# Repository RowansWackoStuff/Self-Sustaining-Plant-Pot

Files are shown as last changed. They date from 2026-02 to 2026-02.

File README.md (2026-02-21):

# SelfSustainingPlantPot
This project is an attempt at making a self watering plant pot that can water plants overtime with custom settings

Goals:
- enough water to last a week
- supplied by battery power
- release water consistently
bonus goals:
- controlled through web server
- setting for watering seeds over time

I wanted to start with a pot that contains the soil and the electronic components, which could have an external silo attached that could be filled with water. The pot diameter has to be at least 15 cm and the height must be 15cm in order for proper root development. With this in mind, a rough sketch can be made.
<div align="center">
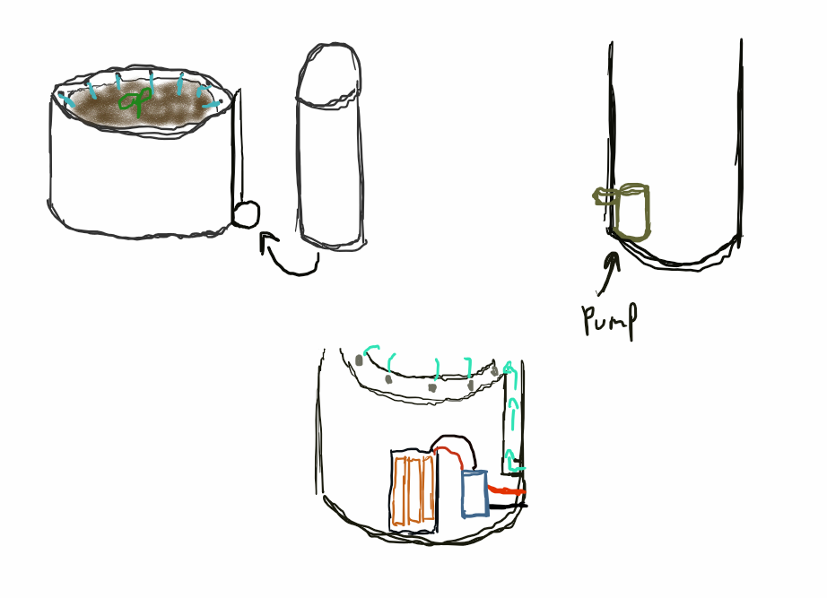
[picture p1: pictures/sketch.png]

</div>

## Piping

The first step was to find out how the water pipe setup would be done. In order to do this i started by testing different pipe hole diameters, number of holes and pipe lengths until I found the desired pressure.

<div align="center">
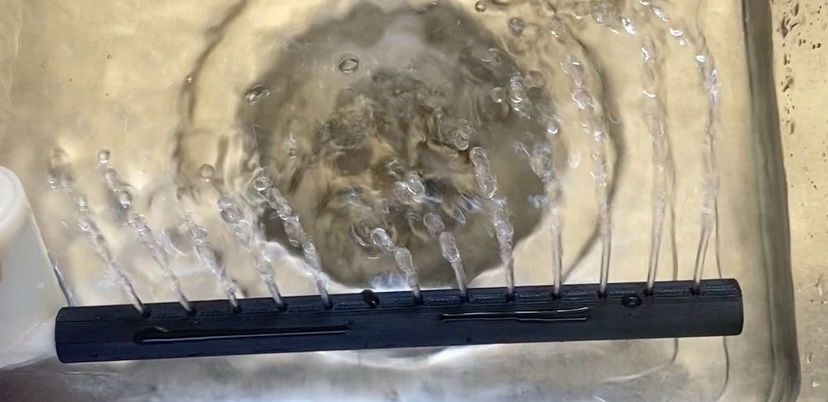
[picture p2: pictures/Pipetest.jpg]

</div>

After some trial and error, the number of holes and diameter were determined and made into a ring.

<div align="center">
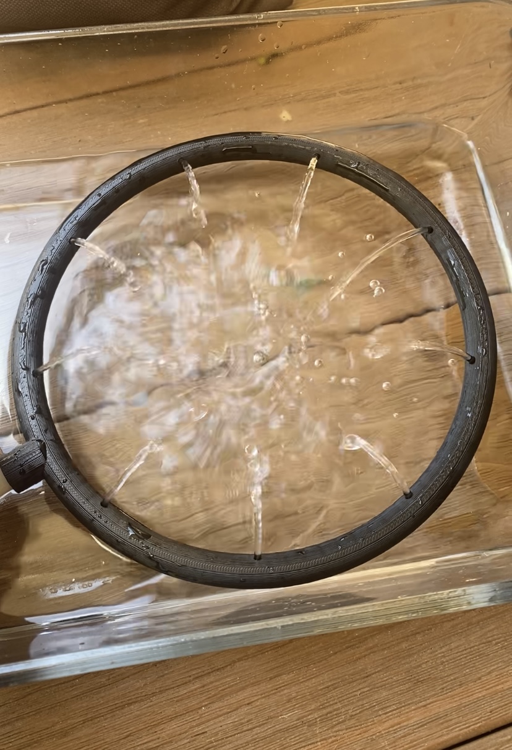
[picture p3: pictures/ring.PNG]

</div>

Adding an extension pipe from the pump to the ring reduces the amount of pressure in the piping, so I assumed I would need to alter the ring's hole's size but the pressure was sustainable enough to travel the distance and exit the holes perfectly.
(This one was a bit over the top.)
<div align="center">
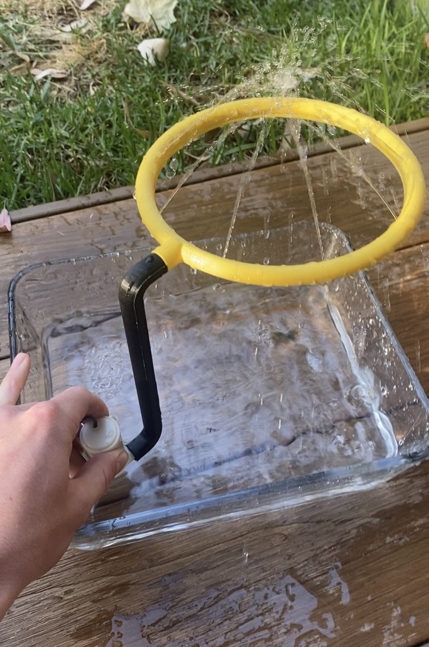
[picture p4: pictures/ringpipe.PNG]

</div>

## Electronics
The electronics involved would have to be a power supply, a microcontroller and a small water pump. For the microcontroller, I chose the ESP32-c3 supermini for its size and web hosting capabilities. 

The power supply for the ESP32 needed a minimum of 3.3V and had to last a long period of time. With the ESP consuming 0.4 mA per hour at most in deep sleep and the estimated time for a lettuce to mature being at most 11 weeks (77 days, 1,848 hours), then the power supply needs 0.004 * 1,848 = 7392 mAh

Using a configuration of 3 AA batteries in series the collective voltage is 4.5V and has a current supply of 8,100mah satisfying the needs of the system

Starting out I used a transistor to deliver 5V to the pump through the board. This setup didn't work due to the poor flow of current through the resistor limiting the output of the water pump.
<div align="center">
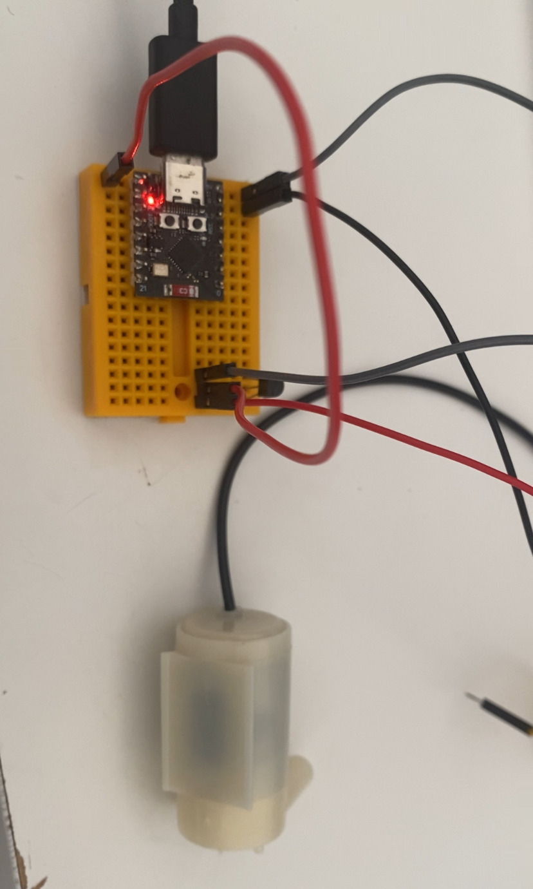
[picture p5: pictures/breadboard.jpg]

</div>

In order to fix this issue, I swapped the transistor for a relay with an external power supply. This solution also solved the voltage drop the ESP was suffering from, which caused it to reset every time the motor turned on.
<div align="center">
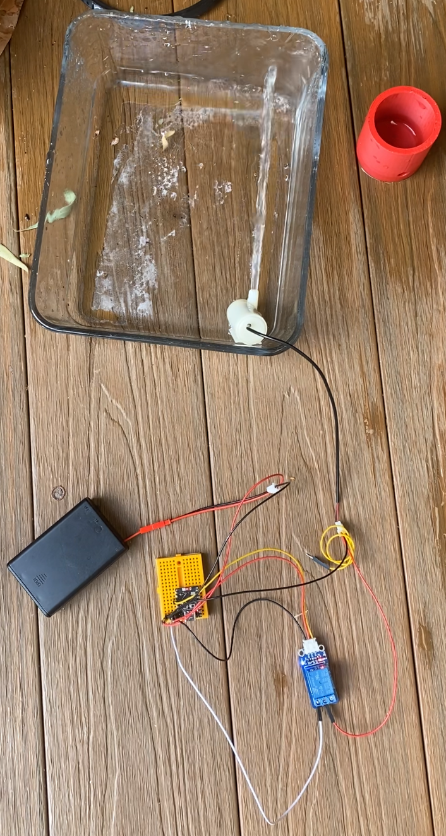
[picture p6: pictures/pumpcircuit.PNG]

</div>

## Programming

In order to interact with the system, I used the ESPAsyncWebServer library, which allowed for the ESP to run an asynchronous web server off its wifi. This wifi can be connected with through any device in order to open a webpage containing the user interface of the system.

This user interface consists of a water setting for default watering a plant daily with the same amount aswell as a seed setting the takes a minimum and maximum amount of water as well as the amount of days to water in order to grow seeds. The seeds are watered exponentially over the day's as in the early stage of development the seeds need a small amount of water, and in the mature stages require a drastically larger amount of water.

<div align="center">
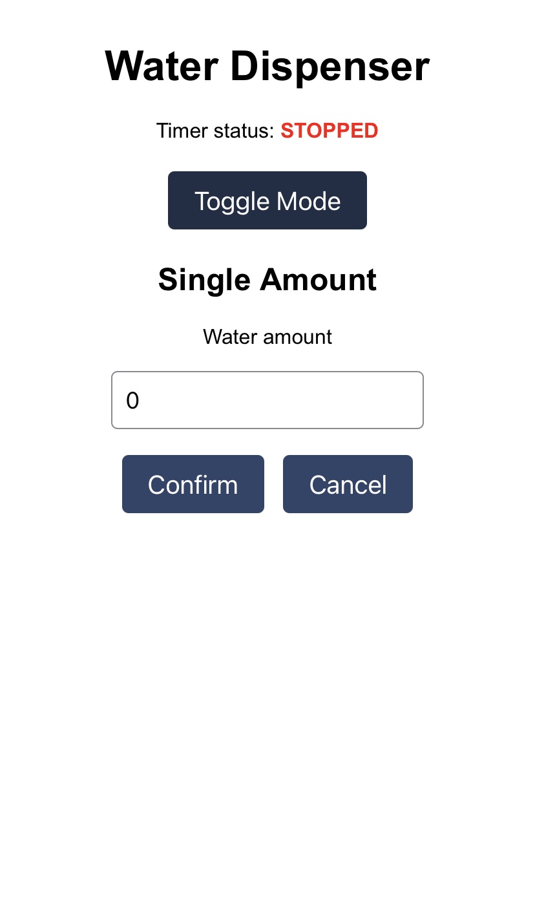
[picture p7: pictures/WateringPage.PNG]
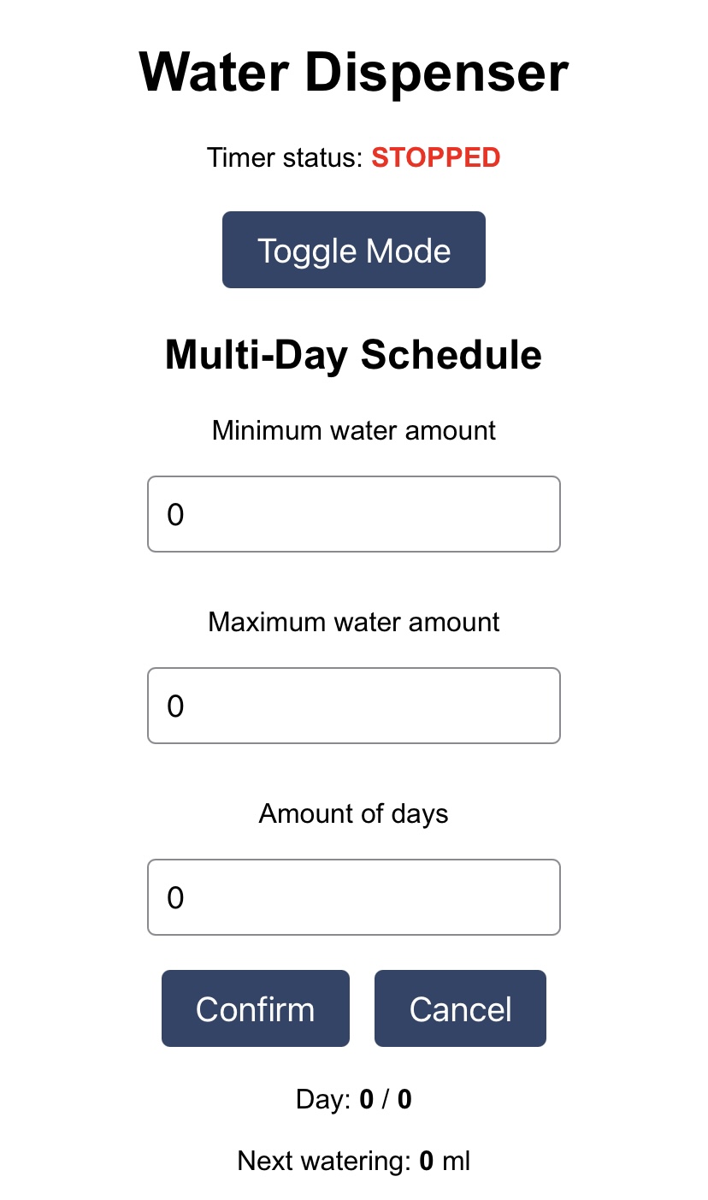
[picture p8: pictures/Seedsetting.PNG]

</div>

Deep sleep is an ultralow power state for microcontrollers that maximizes the amount of battery life when waiting. For the pot, the deep sleep is set once the watering settings are set and the switch for pin 5 is off. This turns off the wifi and other components and sets a 24hr timer for the system to wake up, water, sleep and repeat. With this programming running in the startup script of the esp the system can save power and extend the project's lifetime.

## Testing pot
A small lettuce needs roughly less than 1 cup of water a day for growth. With this in mind, the height of the reservoir can be calculated.

1 cup = 250ml, 7 cups = 1750ml, 1750ml = 1750cm^3, cylinder volume = pi*r^2*h, 1750cm = pi * 7.5^2 * h, h = 9.9cm

With this, the height of the reservoir will be rounded to 10 cm.

I wanted the pot to be modular in order to print in the printer's base of 256x256mm. In order to do this, I split the pipe, ring, reservoir, pot, and electrical components into seperate moduals.

## TEST POT
I printed and tested each part individually and avoided printing the top pot in order to save filiment and instead just printed the base screw and ring mount seperatly.
<div>
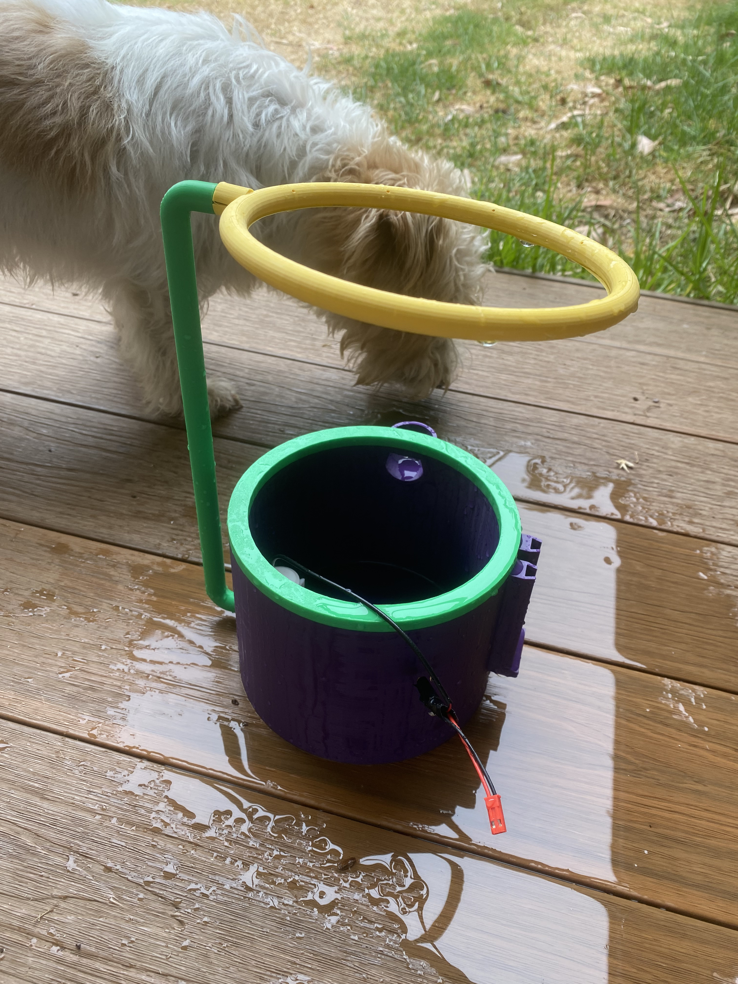
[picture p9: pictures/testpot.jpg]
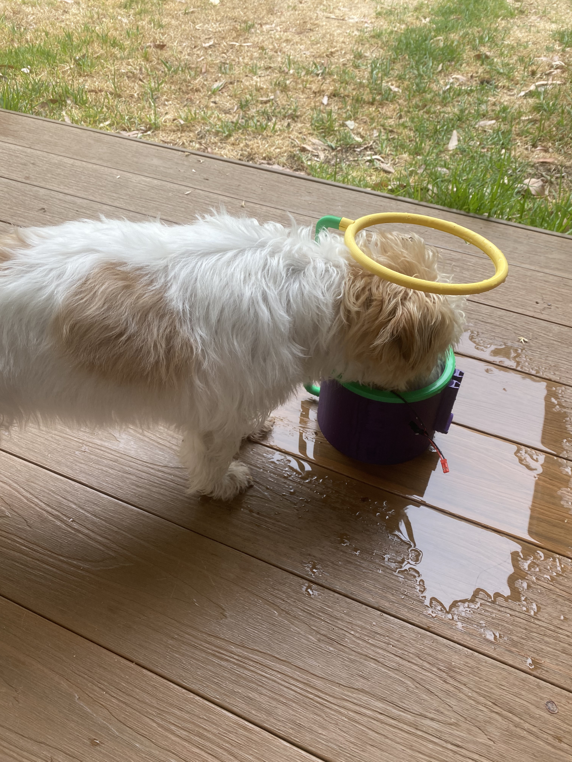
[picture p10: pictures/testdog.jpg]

</div>

## FINAL MODELS

## Ring + Pipe
The ring connects into the top of the pot to keep it still, with the pipe having connections to the reservoir and ring.
<div align="center">
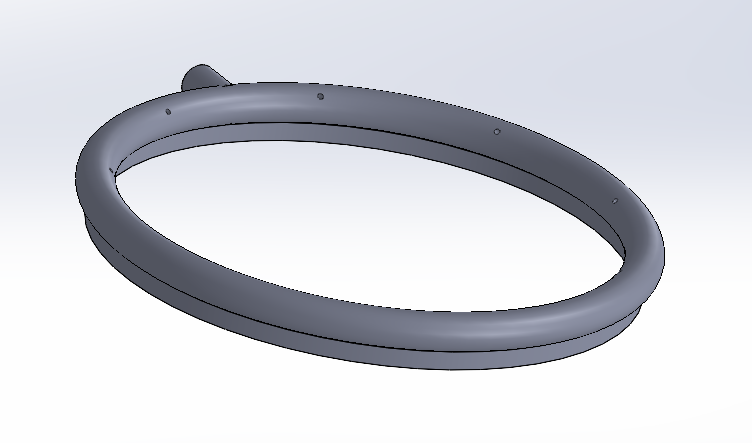
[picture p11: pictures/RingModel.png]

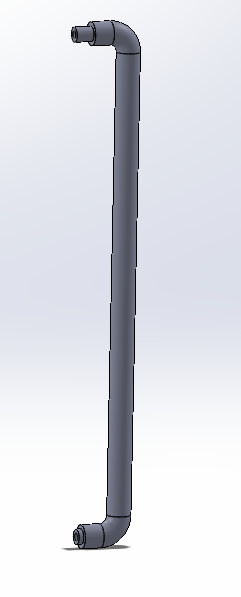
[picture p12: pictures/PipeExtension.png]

</div>

## Top Pot
The top pot has a custom screw base as well as a circular cut in the top to allow for a stable ring connection.
<div align="center">
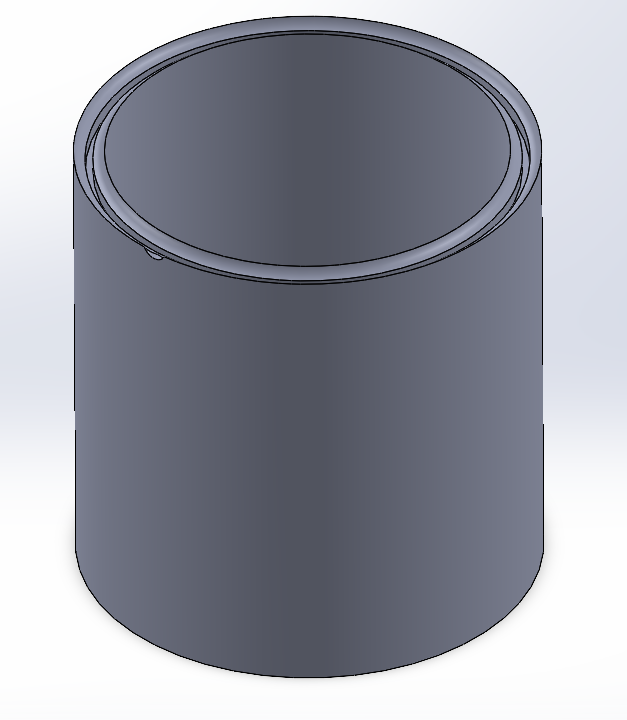
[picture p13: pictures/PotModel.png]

</div>

## Reservoir
The reservoir has the connection to the battery box to slide into as well as a hole for the pump's pipe to slot into.
<div align="center">
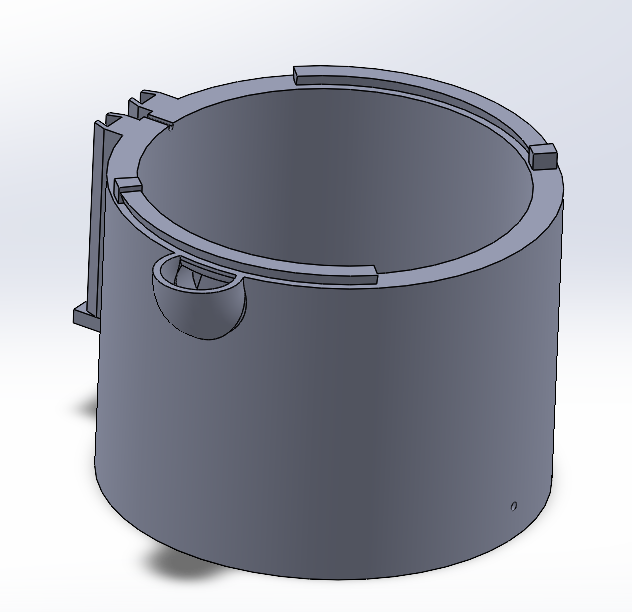
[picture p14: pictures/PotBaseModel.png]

</div>

## Battery Box
The battery box is built of several parts that slide into place with each other before slotting into the reservoir. The battery box has space to hold 6 double A batteries, with the circuit box attaching on top for all the electrical components to sit inside.
<div align="center">
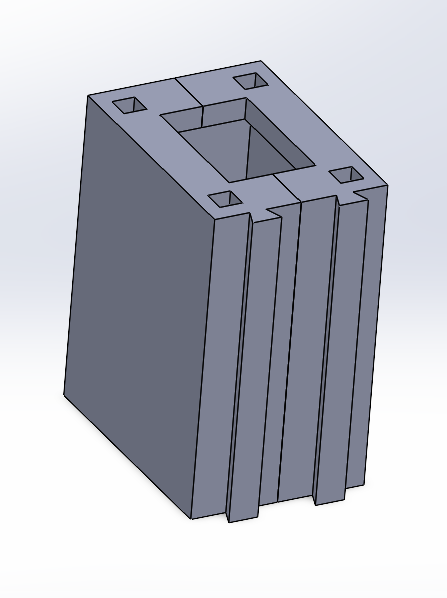
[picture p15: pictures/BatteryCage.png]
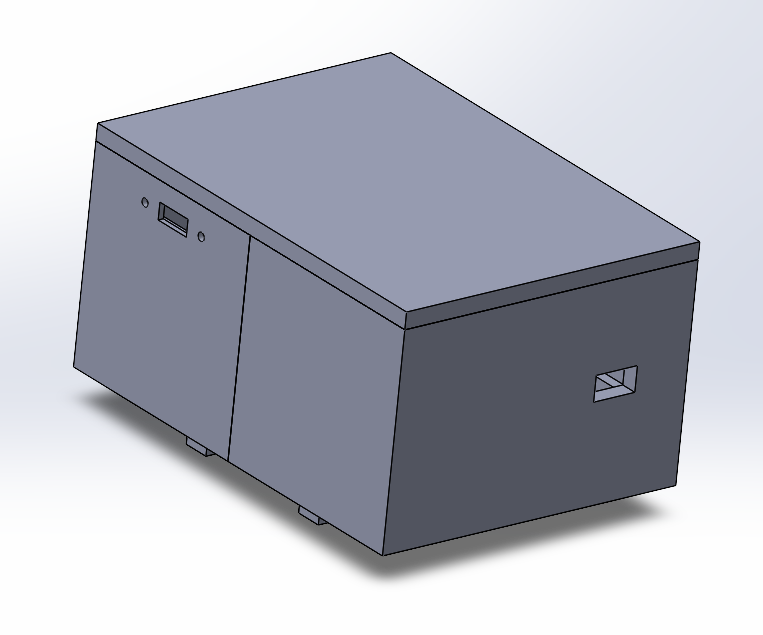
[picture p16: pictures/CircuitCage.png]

</div>

## FINISHED

<div align="center">
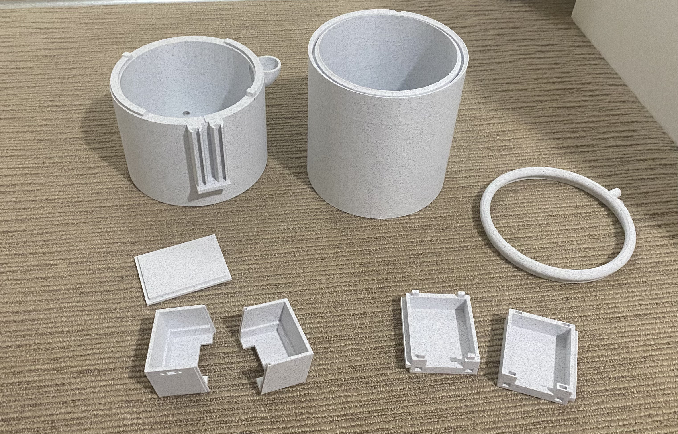
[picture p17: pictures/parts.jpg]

</div>

<div align="center">
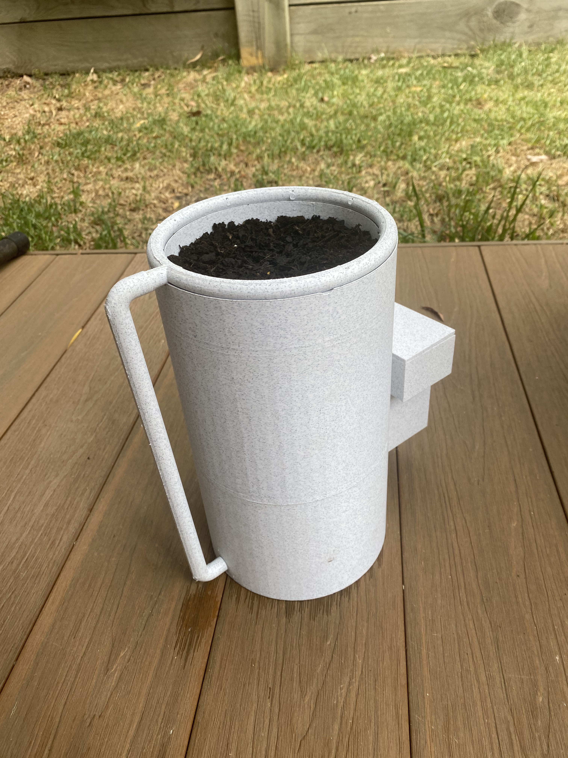
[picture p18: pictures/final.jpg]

</div>

# Conclusion

Goals:
- enough water to last a week ✅
- supplied by battery power ✅
- release water consistently ✅
Bonus goals:
- controlled through web server ✅
- setting for watering seeds over time ✅

# mistakes/problems on the way
- SolidWorks having no export only save as led me to save over my own files multiple times instead of exporting stls
- printed the final prototype base just for it to come out missing the pipe connection in order to not waste filiment printing again I drilled a hole
in the same place, this caused me to have to remake the extension pipe as well as caused the pump to be superglued in place due to it being loose in the hole (wont be making that mistake again)
- the external pipe leaks due to poor sealing
- Tolerance for filiments changed when swapping to the final prototype so testing the connections was a waste of time

# Improvements for Next Time:
- reduce locking seal length (friction is very strong).
- get external clock from the esp as the esp couldn't track how longs it's slept for.
- improve seals for water pipes.
- Incorporate pipe into waterpot for better aesthetic.
- Create a custom PCB to reduce soldering errors.
- Battery box clips separated (need to learn better techniques)
- Sort SolidWorks files neatly in order to reduce complications
  
I'll update this page with the lettuce growth once complete (if ever).

THANKS FOR READING!

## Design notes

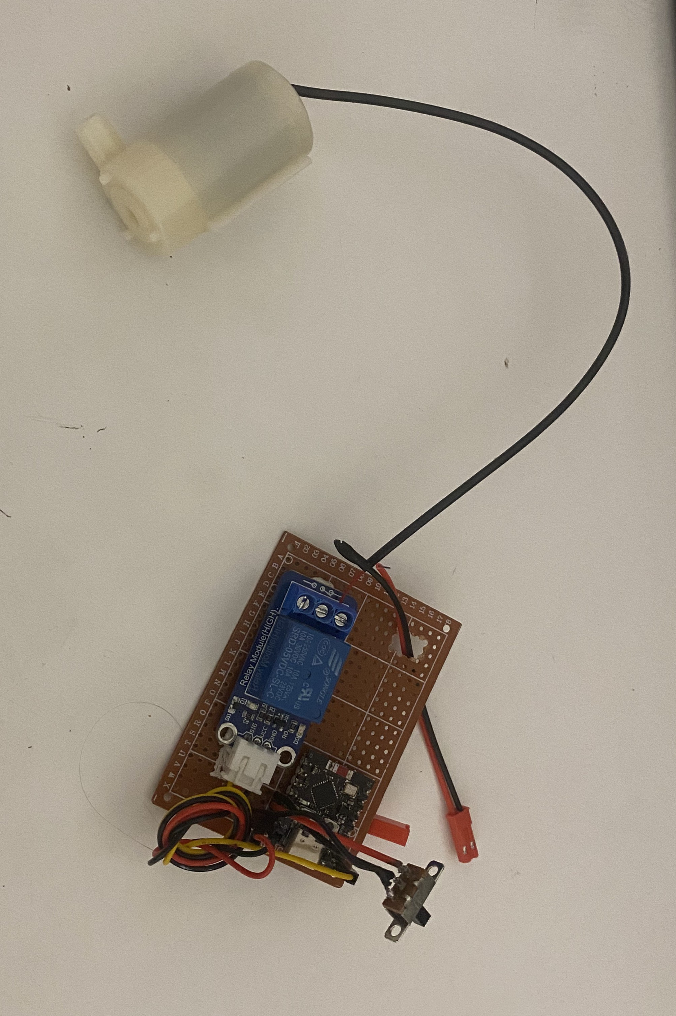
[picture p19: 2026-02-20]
pictures/circuit.jpg

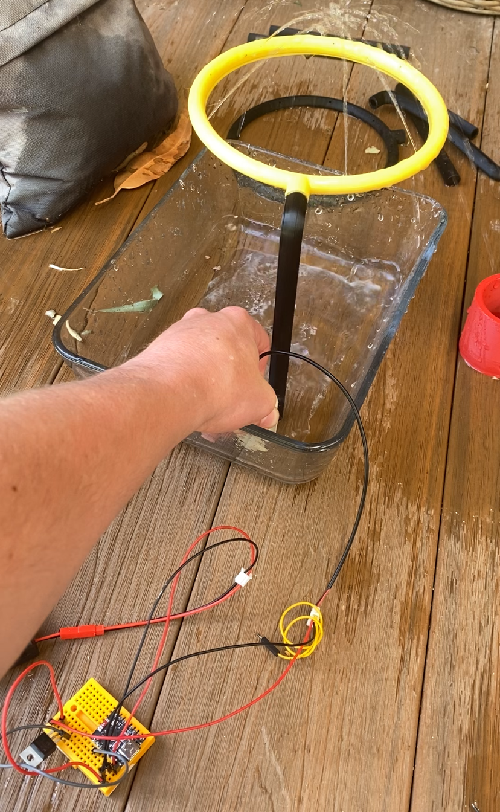
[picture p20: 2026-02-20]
pictures/ringpipecircuit.PNG

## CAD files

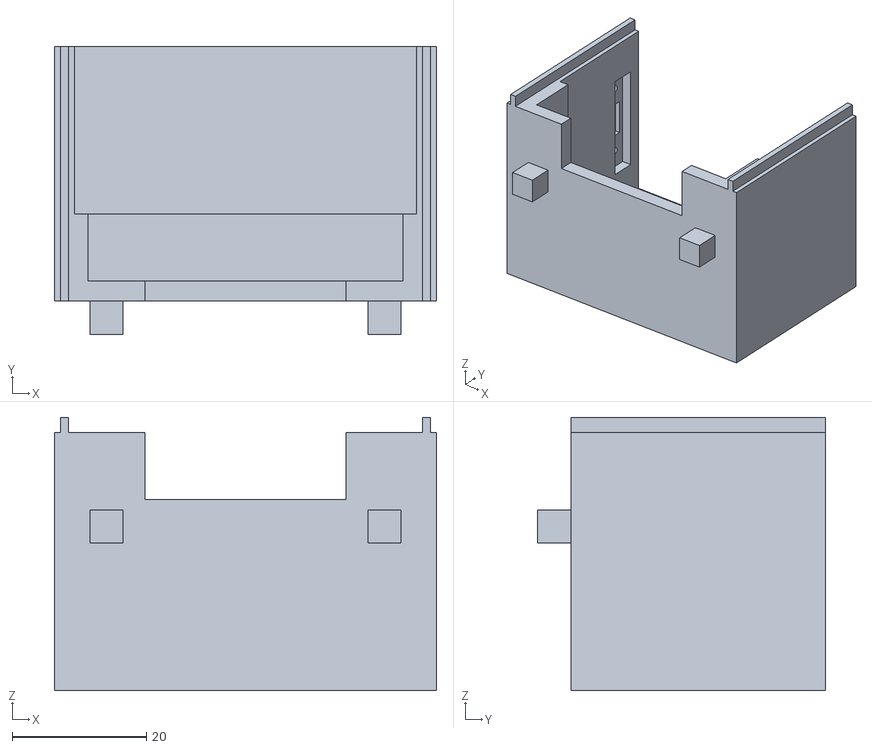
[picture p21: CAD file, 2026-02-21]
SolidWorksFiles/CircuitCage1.STL
57.0 x 43.0 x 40.8

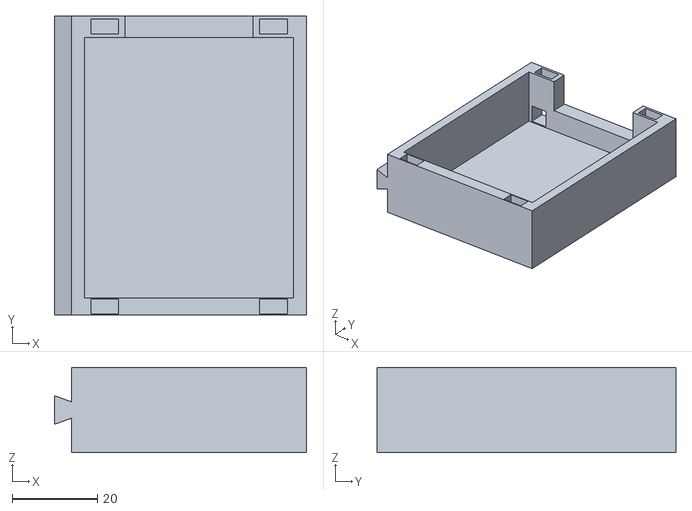
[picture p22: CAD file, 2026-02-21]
SolidWorksFiles/BatteryCage1.STL
59.0 x 70.0 x 20.0

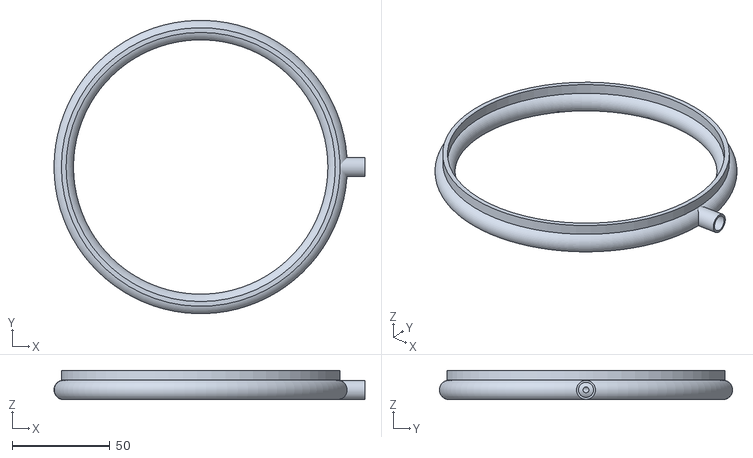
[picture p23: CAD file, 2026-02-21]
SolidWorksFiles/ringTest10.STL
159.0 x 149.9 x 15.0

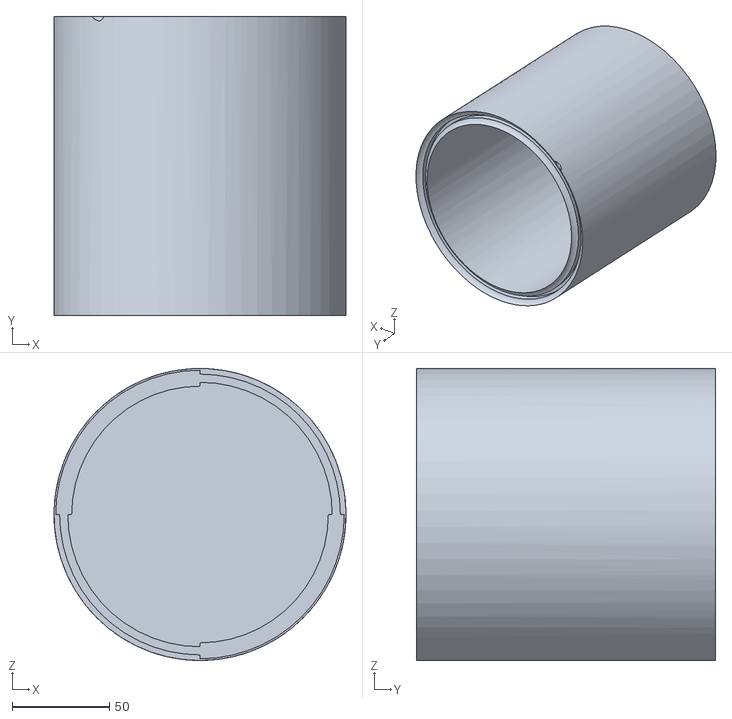
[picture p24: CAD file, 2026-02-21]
SolidWorksFiles/PotTopFINAL.STL
150.0 x 153.7 x 150.0

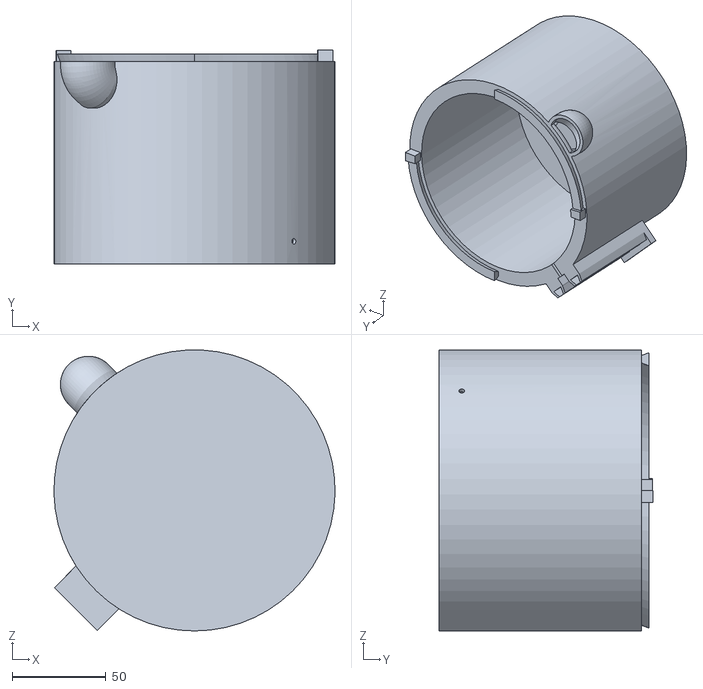
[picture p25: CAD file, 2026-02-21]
SolidWorksFiles/PotBaseTest.STL
149.9 x 114.0 x 149.9

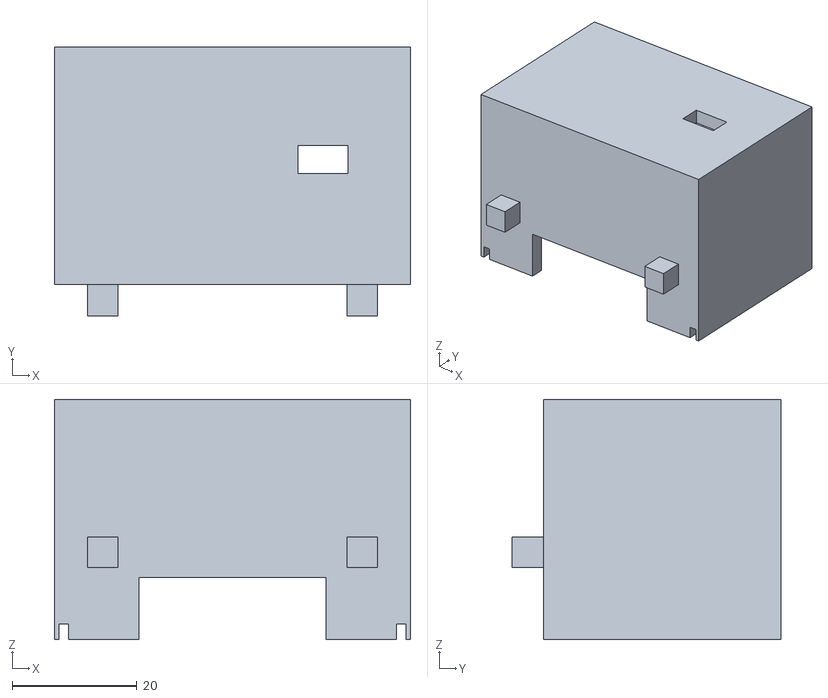
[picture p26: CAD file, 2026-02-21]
SolidWorksFiles/CircuitCage2.STL
57.0 x 43.0 x 38.5

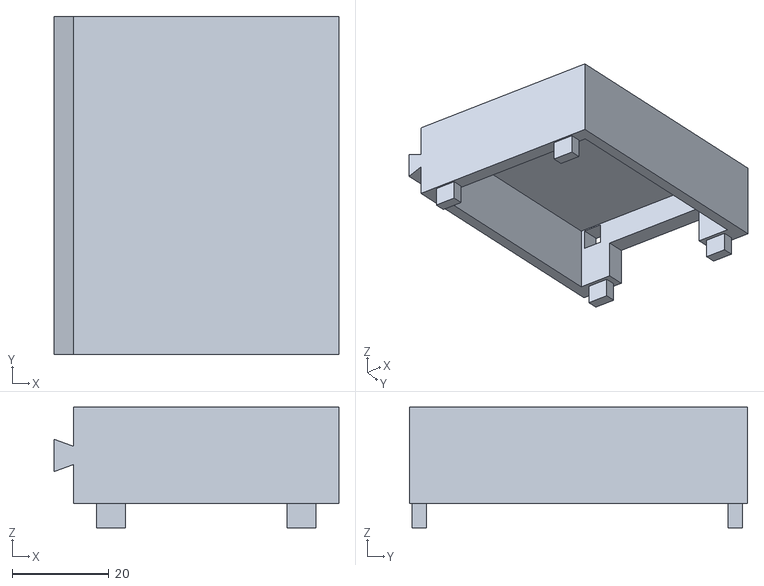
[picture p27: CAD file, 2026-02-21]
SolidWorksFiles/BatteryCage2.STL
59.0 x 70.0 x 25.0

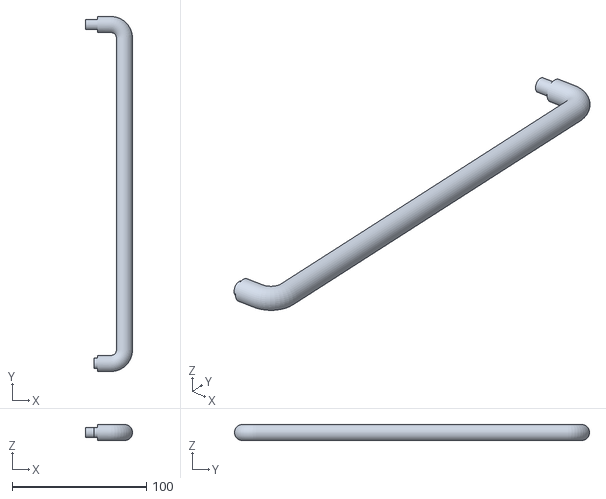
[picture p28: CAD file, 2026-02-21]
SolidWorksFiles/pipeExtensionFIX2.STL
35.0 x 264.0 x 12.0

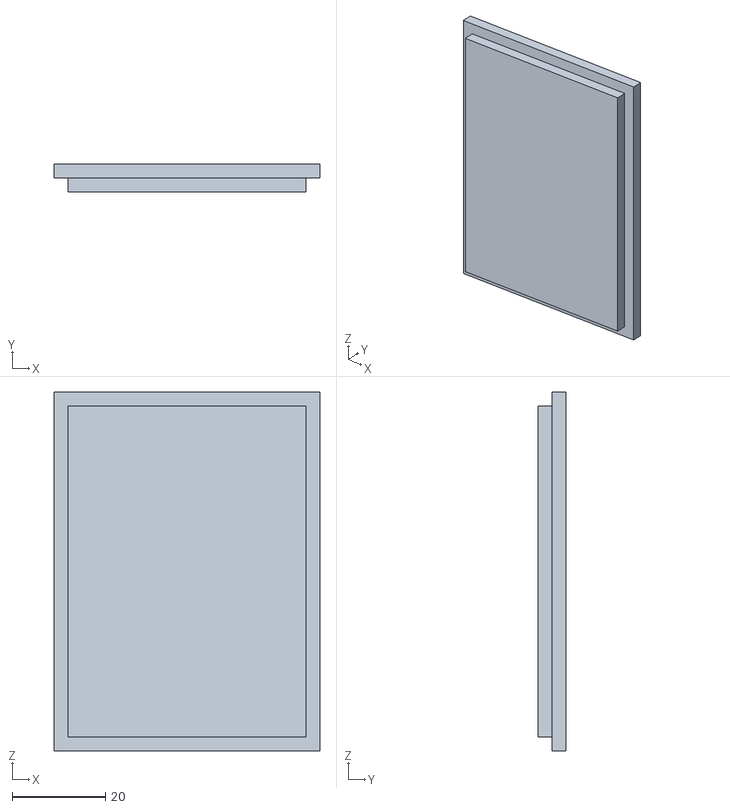
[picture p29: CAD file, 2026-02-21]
SolidWorksFiles/CircuitCage3.STL
57.0 x 6.00 x 77.0

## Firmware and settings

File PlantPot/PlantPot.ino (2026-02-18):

#include <Arduino.h>
#include "esp_sleep.h"

#include <WiFi.h>
#include <AsyncTCP.h>
#include "esp_sleep.h"
#include <ESPAsyncWebServer.h>

#define BUTTON_PIN 4 // RTC-capable pin

const int pumpPin = 5; 

bool pumpRunning = false;
unsigned long pumpStopTime = 0;

const unsigned long TIMER_24H = 24UL * 60ULL * 60ULL * 1000000ULL;
// const unsigned long TIMER_24H = 15ULL * 1000000ULL;

RTC_DATA_ATTR double waterAmount = 0;
RTC_DATA_ATTR double maxWaterAmount = 0;
RTC_DATA_ATTR double days = 0;
RTC_DATA_ATTR double currentDay = 0;
RTC_DATA_ATTR bool seedSettingActive = false;
RTC_DATA_ATTR bool timer24hActive = false;

// HTML web page
const char index_html[] PROGMEM = R"rawliteral(
<!DOCTYPE HTML><html>
<head>
  <title>ESP Water Control</title>
  <meta name="viewport" content="width=device-width, initial-scale=1">
  <style>
    body { font-family: Arial; text-align: center; margin:0 auto; padding-top: 20px;}
    input {
      padding: 10px;
      font-size: 18px;
      width: 220px;
      margin-bottom: 15px;
    }
    .button {
      padding: 10px 20px;
      font-size: 20px;
      color: #fff;
      background-color: #2f4468;
      border: none;
      border-radius: 5px;
      cursor: pointer;
      margin: 5px;
    }
    .button:hover { background-color: #1f2e45; }
    .hidden { display: none; }
  </style>
</head>
<body>
  <h1>Water Dispenser</h1>

  <p>
    Timer status:
    <strong id="timerStatus" style="color:red;">STOPPED</strong>
  </p>

  <button class="button" onclick="togglePage()">Toggle Mode</button>

  <!-- PAGE 1 -->
<div id="pageSingle">
  <h2>Single Amount</h2>
  <p>Water amount</p>
  <input type="number" id="amount" min="1" value="%MIN_WATER%">
  <br>
  <button class="button" onclick="sendAmount()">Confirm</button>
  <button class="button" onclick="cancel()">Cancel</button>
</div>

<!-- PAGE 2 -->
<div id="pageMulti" class="hidden">
  <h2>Multi-Day Schedule</h2>

  <p>Minimum water amount</p>
  <input type="number" id="amount1" min="1" value="%MIN_WATER%"><br>
  <p>Maximum water amount</p>
  <input type="number" id="amount2" min="1" value="%MAX_WATER%"><br>
  <p>Amount of days</p>
  <input type="number" id="days" min="1" value="%DAYS%"><br>

  <button class="button" onclick="sendMulti()">Confirm</button>
  <button class="button" onclick="cancel()">Cancel</button>

  <div id="seedStatus" style="margin-bottom:15px;">
    <p>
      Day:
      <strong id="currentDay">0</strong> /
      <strong id="totalDays">0</strong>
    </p>
    <p>
      Next watering:
      <strong id="nextWater">0</strong> ml
    </p>
  </div>

</div>

<script>
let showingSingle = true;

function sendAmount() {
  var amount = document.getElementById("amount").value;
  if (amount === "") {
    alert("Please enter an amount");
    return;
  }
  var xhr = new XMLHttpRequest();
  xhr.open("GET", "/water?amount=" + amount, true);
  xhr.onload = updateStatus;
  xhr.send();
}

function sendMulti() {
  var a1 = document.getElementById("amount1").value;
  var a2 = document.getElementById("amount2").value;
  var d  = document.getElementById("days").value;

  if (a1 === "" || a2 === "" || d === "") {
    alert("Fill all fields");
    return;
  }

  var xhr = new XMLHttpRequest();
  xhr.open("GET",
    "/water_multi?amount1=" + a1 + "&amount2=" + a2 + "&days=" + d,
    true
  );
  xhr.onload = updateStatus;
  updateSeedStatus();
  xhr.send();
}

function cancel() {
  var xhr = new XMLHttpRequest();
  xhr.open("GET", "/cancel", true);
  xhr.onload = updateStatus;
  updateSeedStatus();
  xhr.send();
}


function updateStatus() {
  var xhr = new XMLHttpRequest();
  xhr.open("GET", "/status", true);
  xhr.onload = function () {
    if (xhr.status === 200) {
      var data = JSON.parse(xhr.responseText);
      var el = document.getElementById("timerStatus");
      el.textContent = data.running ? "RUNNING" : "STOPPED";
      el.style.color = data.running ? "green" : "red";
    }
  };
  xhr.send();
}

function updateSeedStatus() {
  var xhr = new XMLHttpRequest();
  xhr.open("GET", "/seed_status", true);
  xhr.onload = function () {
    if (xhr.status === 200) {
      var data = JSON.parse(xhr.responseText);

      if (!data.active) return;

      document.getElementById("currentDay").textContent = data.currentDay;
      document.getElementById("totalDays").textContent = data.days;
      document.getElementById("nextWater").textContent = data.nextWater;
    }
  };
  xhr.send();
}

window.onload = function () {
  updateStatus();
  updateSeedStatus();
};

function togglePage() {
  showingSingle = !showingSingle;
  document.getElementById("pageSingle").classList.toggle("hidden");
  document.getElementById("pageMulti").classList.toggle("hidden");

  if (!showingSingle) {
    updateSeedStatus();
  }
}

</script>
</body>
</html>
)rawliteral";

String templateProcessor(const String& var) {
  if (var == "MIN_WATER") {
    return waterAmount > 0 ? String(waterAmount, 0) : "0";
  }
  if (var == "MAX_WATER") {
    return maxWaterAmount > 0 ? String(maxWaterAmount, 0) : "0";
  }
  if (var == "DAYS") {
    return days > 0 ? String(days, 0) : "0";
  }
  if (var == "TIMER_STATUS") {
    return timer24hActive ? "RUNNING" : "STOPPED";
  }
  if (var == "TIMER_COLOR") {
    return timer24hActive ? "green" : "red";
  }
  return "";
}

void goToDeepSleep() {
  esp_sleep_disable_wakeup_source(ESP_SLEEP_WAKEUP_ALL);

  // Timer wakeup
  if(timer24hActive == true){
    esp_sleep_enable_timer_wakeup(TIMER_24H);
  }

  // specify which pin wakes the esp
  uint64_t mask = 1ULL << BUTTON_PIN;
  // esp_deep_sleep_enable_gpio_wakeup(mask, ESP_GPIO_WAKEUP_GPIO_LOW);
  esp_deep_sleep_enable_gpio_wakeup(mask, ESP_GPIO_WAKEUP_GPIO_HIGH);

  // enter deep sleep
  digitalWrite(pumpPin, LOW); // just in case
  Serial.println("Entering deep sleep...");
  delay(100);
  esp_deep_sleep_start();
}



void runWaterFunction(int amountML) {
  Serial.print("Water requested: ");
  Serial.print(amountML);
  Serial.println(" mL");

  // set water amount so that the pump can be repeated by the timer
  waterAmount = amountML;
  // calculate amount of time to run the pump 
  unsigned long runTime = amountML/22.0  * 1000;

  // set pump duration + extra time for water to flow through pipe
  pumpStopTime = millis() + runTime + 500;
  pumpRunning = true;
  digitalWrite(pumpPin, HIGH);

  // 80,000 * (t * 60 * 60) = 500 mililitrers a hour
  // 22ml a second
}

void notFound(AsyncWebServerRequest *request) {
  request->send(404, "text/plain", "Not found");
}

AsyncWebServer server(80);

void enableWebserver(){
  WiFi.mode(WIFI_AP);
  WiFi.softAP("MyESP32_AP", "12345678");

  IPAddress IP = WiFi.softAPIP();
  Serial.print("Connect to Wi-Fi at: http://");
  Serial.println(IP);
  
  // Send web page to client
  server.on("/", HTTP_GET, [](AsyncWebServerRequest *request){
    request->send_P(200, "text/html", index_html, templateProcessor);
  });

  server.on("/water", HTTP_GET, [](AsyncWebServerRequest *request) {
    if (request->hasParam("amount")) {

      // water
      int amount = request->getParam("amount")->value().toInt();
      // waterAmount = amount;
      
      // begin water timer
      timer24hActive = true;

      // ensure seed setting is no longer active
      seedSettingActive = false;
      
      request->send(200, "text/plain", "Water amount received");

      runWaterFunction(amount);

    } else {
      request->send(400, "text/plain", "Missing amount");
    }
  });

  server.on("/water_multi", HTTP_GET, [](AsyncWebServerRequest *request) {
    if (request->hasParam("amount1") && request->hasParam("amount2") && request->hasParam("days")) {

      // store varaibles
      waterAmount = request->getParam("amount1")->value().toInt();
      maxWaterAmount = request->getParam("amount2")->value().toInt();
      days = request->getParam("days")->value().toInt();
      currentDay = 0;
      
      // begin water timer
      timer24hActive = true;

      // ensure seed setting is active
      seedSettingActive = true;
      
      request->send(200, "text/plain", "Water amount received");
      
      runWaterFunction(waterAmount);

    } else {
      request->send(400, "text/plain", "Missing amount");
    }
  });

  server.on("/cancel", HTTP_GET, [](AsyncWebServerRequest *request) {

    // cancel timer and pump
    timer24hActive = false;
    pumpStopTime = 0;
    pumpRunning = false;
    digitalWrite(pumpPin, LOW);

    request->send(200, "text/plain", "Cancelled");
  });

  server.on("/status", HTTP_GET, [](AsyncWebServerRequest *request) {
    String json = "{ \"running\": ";
    json += timer24hActive ? "true" : "false";
    json += " }";
    request->send(200, "application/json", json);
  });

  server.on("/seed_status", HTTP_GET, [](AsyncWebServerRequest *request) {
    String json = "{";
    json += "\"active\":"; json += seedSettingActive ? "true" : "false";
    json += ",\"currentDay\":"; json += String(currentDay, 0);
    json += ",\"days\":"; json += String(days, 0);
    json += ",\"nextWater\":"; json += String(waterAmount, 0);
    json += "}";

    request->send(200, "application/json", json);
  });
  
  server.onNotFound(notFound);
  server.begin();
}

void setup() {
  Serial.begin(115200);
  delay(1000); // wait for Serial Monitor to connect on startup

  // enable pins
  pinMode(BUTTON_PIN, INPUT_PULLUP); // Button to GND
  // pinMode(BUTTON_PIN, INPUT); // Button to GND
  pinMode(pumpPin, OUTPUT);
  digitalWrite(pumpPin, LOW);

  esp_sleep_wakeup_cause_t reason = esp_sleep_get_wakeup_cause();
  if (reason == ESP_SLEEP_WAKEUP_GPIO) {
    Serial.println("Woke up from button press!");
    enableWebserver();
    Serial.println("Webserver running");
  } 
  else if (reason == ESP_SLEEP_WAKEUP_TIMER) {
    // water plants
    if(seedSettingActive == false){
      runWaterFunction(waterAmount);
    }
    else{
      if(currentDay < days){
        currentDay++;

        Serial.print("day: ");
        Serial.print(currentDay);
        Serial.println("");

        // exponential calculation
        // R = (B/A)^(1/T) - 1
        // B = future value (max water)
        // A = original value (min water)
        // R = growth rate ()
        // T = time period (days)
        double growthRate = pow((maxWaterAmount/waterAmount),(currentDay/days)) - 1;

        Serial.print("growth rate: ");
        Serial.print(growthRate);
        Serial.println("");

        waterAmount = waterAmount + (waterAmount * growthRate);

        Serial.print("water amount: ");
        Serial.print(waterAmount);
        Serial.println("");
      }

      runWaterFunction(waterAmount);
    }
    
    // go back to sleep
    // goToDeepSleep();
  }
  else {

    // if the switch is on while batteries are plugged in then keep website on
    if (digitalRead(BUTTON_PIN) == LOW) {
      Serial.println("Power-on or reset. Waiting 3 sec before sleep...");
      delay(3000); // <-- Give time to open Serial Monitor
      goToDeepSleep();
    }
    else if (digitalRead(BUTTON_PIN) == HIGH){
      enableWebserver();
      Serial.println("Webserver running");
    }

    
  }

  Serial.println("Device awake. Press button to sleep again.");
}

void loop() {
  // stop pumping water once timer is up
  if (pumpRunning && millis() >= pumpStopTime){
    digitalWrite(pumpPin, LOW);
    pumpRunning = false;
    Serial.println("Pump stopped");

    if(digitalRead(BUTTON_PIN) == LOW){
      goToDeepSleep();
    }
  }
  
  // go to sleep once button pressed
  if (digitalRead(BUTTON_PIN) == LOW && pumpRunning == false) {
    goToDeepSleep();
  }

}

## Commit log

2026-01-24 added arduino file
    this file has the basics for running an esp webserver which contains buttons for setting the watering amount, a timer for watering and a cancel button
2026-01-28 webserver on button press, button and timer wake up esp
    only problem is the remaining time is janked up and giving a crazy number
    [PlantPot.ino]
2026-01-30 removed remaining timer due to deep sleep difficulties
2026-02-05 moved pump loops out of web server functions
    DONT PUT LOOPS IN WEB STATEMENTS
2026-02-18 24 hour timer enabled ready for final prototype
2026-02-21 added solidworks files and photos
    [BatteryCage1.STL, BatteryCage2.STL, CircuitCage1.STL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]
